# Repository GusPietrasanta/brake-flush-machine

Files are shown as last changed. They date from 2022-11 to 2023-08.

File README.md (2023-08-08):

# Brake Fluid Flush Machine

Brake Fluid Flush Machine is a personal project that was born in the need to replace an old and unfunctional PCB that controlled all the functions in an ATE FB30S.

All the mechanical parts of the machine were working perfectly, but the PCB broke down, not being able to control the output pressure anymore, going to full pressure constantly. That resulted in the necessity of a person (me, ha) continually controlling the pressure manually, simply and boringly turning the knob on and off, while flushing the brake fluid of the cars at the shop were I work.

Due to the age of the machine, spare parts are not longer available, making it impossible to buy a replacement PCB.

The original PCB had to be completely replaced for a hand-made circuit board that houses a STM32F103C6T6 (A.K.A. BluePill) as the brain of the machine. Also minor additions and modifications had to be done to the original wiring and components.

## How it works

Schematics for the wiring can be found in the schematics folder of the project (both .kicad files and screen captures for quick reference).

The C code is pretty simple and straightforward, and also heavily commented, but basically it runs a program which:

1. Includes all the start-up functions.
2. Declares 3 constants that correspond to three different settings of pressure (0.4, 1.5 and 2.2 bar) after the ADC (Analog to digital converter).
3. Sets the interval for an alarm/buzzer that is triggered when something is wrong (brake fluid tank level too low, or pressure out of normal values).
4. Initializes variables for brake fluid tank level and pressure.
5. Declares the functions to check if everything is ready to run, check level, and detect the required pressure from the knob.
6. Calls all the start-up functions (clock configuration, PWM Configuration, ADC configuration, enable and start.
7. Initilizes the variables pwm (%/duty for the pump), setPoint (or desired pressure), error (setPoint - pressure) and timerBuzzer to 0.
8. Starts the infinite loop which:
  - Checks if everything is ok to run (pressure reading and tank level).
    - If so, it turns on the safety relay that feeds the pump, checks the required pressure, calculates the adequate PWM, and sets that PWM to the output pin that controls the pump.
    - If something goes wrong, it sets the PMW to 0, turns the relay off, turns the red LED on, the green LED off, and starts a counter to turn the buzzer on and off.

## Now some images
<div align="center">
 
 ## The problem with the original circuit board.
 The old PCB was dangerously ramping the pressure up constantly beyond safe limits.
 Too much pressure
 
 ## Prototyping at home.
 Prototyping at home
  
 ## The old PCB ready to come out.
Old PCB

## The new circuit board ready to go in (not the final version sadly)
New PCB first version
 
After a couple of runs, the main transistor overheated and stopped working properly: a junction went short-circuit, sending the pump to full speed. The safety relay came into action turning the power supply off avoiding a probable explosion of the plastic reservoir for the brake fluid of the car I was working on at the moment, due to over-pressure.
  
Time to see what happened.
 
## Wrong power transistor handling = Long fall time = Overheating
  
On the first version of the circuit board I was using a pre-made MOSFET driver module that was near to its current limits, plus a way too high frequency choice to avoid noise from DC motor.
  
 Long transistor fall time

 ## Lower frequency + using an optocoupler with the right resistor = Perfect.
  
 Now with some changes done to the transistor driving circuit and modifiying the code to run the PWM at 1kHz instead of 10kHz made a nice waveform.
  
Better transistor fall time
  
 ## Fitting the new version of the circuit board.
  
  Fitting the circuit baord
  
 ## Testing the 3 different pressure settings.
  
  Testing pressure
  
## Brake fluid level in the tank going low.
  
(Note the pressure manometer dropping to 0 and the red LED turning on while the green one turns off, as well as the brake fluid stops coming out from the fitting of course).
  
  Low level testing

</div>

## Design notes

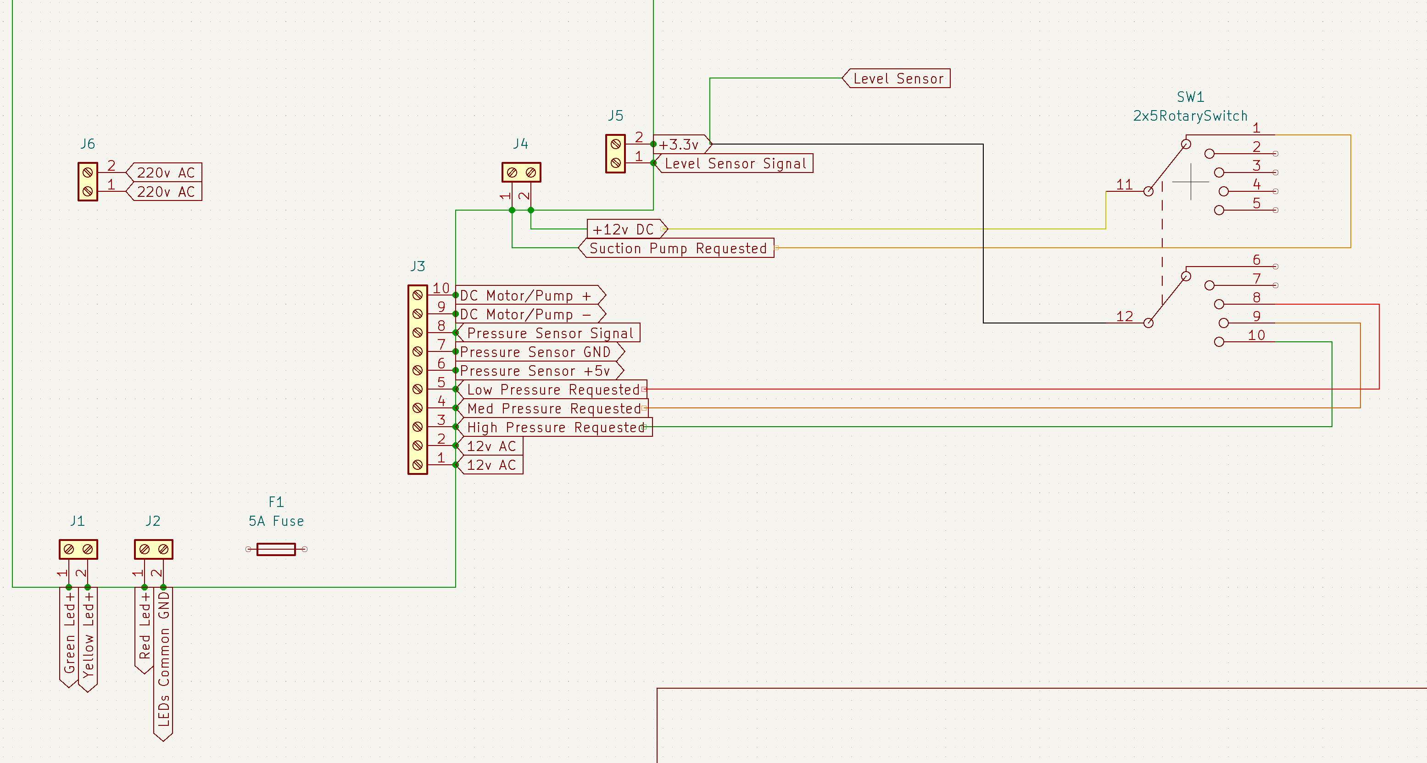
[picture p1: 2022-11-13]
schematics/PinoutBFMBoard/PinoutBFMBoard.png

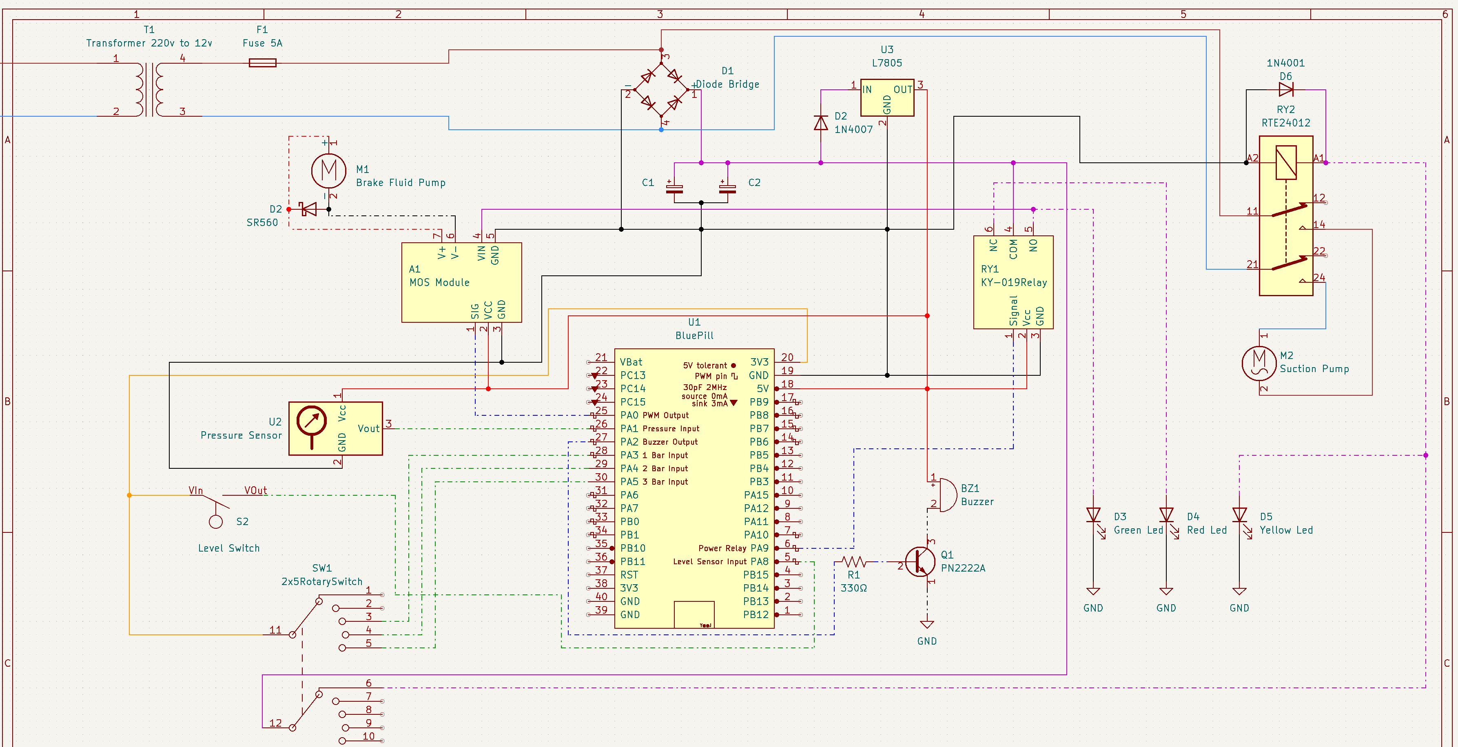
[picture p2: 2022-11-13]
schematics/BrakeFluidMachineSchematics.png

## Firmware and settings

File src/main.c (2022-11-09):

#include "includes.h"

// The next values are ADC values that correspond to 1, 2 and 3 bars of pressure.
const uint16_t oneBar = 800;
const uint16_t twoBar = 1100;
const uint16_t threeBar = 1400;

// This value stores how often the buzzer will toggle (in 10^(-4)/0.1ms increments).
const uint16_t toggleInterval = 10000;

volatile uint8_t levelOk = 0;       // Brake fluid tank level
volatile uint16_t pressure = 0;     // Process Variable/Actual Pressure

// Function that will check if everything is in order to work
uint8_t allGood(void);
// Function that will check the tank level accessing the Port A Pin 8 Input Data Register
uint8_t checkLevel(void);
// Function that will update the set point based on the position of the knob
uint16_t requiredPressure(void);

int main(void)
{
    // Initial configuration functions
  	systemClockConfig();
	pwmConfig();
	gpioConfig();
    adcConfig();
    adcEnable();
    adcStart(1);
	
	volatile uint16_t pwm = 0;          // Control Variable/PWM
    volatile uint16_t setPoint = 0;     // Set Point/Desired pressure
    volatile int16_t error = 0;         // Set Point - Process Variable
    volatile uint16_t timerBuzzer = 0;  // Counter to toggle the buzzer 

    while (1)
	{

        //levelOk = checkLevel();     // Check if the tank level is ok and set as variable

        //pressure = adcGetVal();                     // Get the actual pressure from the ADC

        // If brake fluid tank level is ok, and the pressure sensor is between expected/normal values...
        if (allGood())
        {
            TIM2->CCR3 = 0;                         // Turn the buzzer OFF

            GPIOA->ODR &= ~GPIO_ODR_ODR7;           // Turn red led OFF

            GPIOA->ODR |= GPIO_ODR_ODR6;            // Turn green led ON

            GPIOA->ODR |= GPIO_ODR_ODR9;            // Turn on the power relay that feeds the motor driver

            // While everything is in order...
            while (allGood())
            {
                setPoint = requiredPressure();          // Update the set point to the selected pressure on the machine front knob

                error = setPoint - pressure;            // Calculate the error

                pwm = error * 0.2;                      // Calculate PWM duty - 0.2 is kp/Proportional gain

                if ((pwm > 20) & (pwm < 100))
                {
                    TIM2->CCR1 = pwm;                   // Set the value calculated on pwm as the timer duty cycle
                }
                else if (pwm > 100)
                {
                    TIM2->CCR1 = 100;                   // If calculated value is bigger than 100, set it at 100% (Maximum duty)
                }
                else
                {
                    TIM2->CCR1 = 0;                     // If calculated value is smaller than 0, leave it at 0% (Minimum duty)
                }
            }
        }
        // If conditions were not met...
        else
        {
            GPIOA->ODR &= ~GPIO_ODR_ODR9;            // Turn off the power relay that feeds the motor driver

            GPIOA->ODR &= ~GPIO_ODR_ODR6;           // Turn green led ON

            GPIOA->ODR |= GPIO_ODR_ODR7;            // Turn red led OFF

            pwm = 0;                                // Set PWM to 0%

            TIM2->CCR1 = pwm;                       // Set time Duty Cycle to 0%

            timerBuzzer = toggleInterval - 500;     // Force the timer to be close to 9999 to start as soon as possible.

            /* Here I'm using Timer 2 Update Interrupt Flag as a timer. 
            I don't expect this method to be 100% accurate but it's enough to toggle...
            ... a buzzer on and off, non-blocking, and without activating another Timer.  
            TIM2 UIF is set to 1 by hardware every time TIM2 CNT reaches TIM2 ARR (100)
            Being TIM2 frequency = 1Mhz, CNT will be increased each uS, and TIM2 UIF...
            ... will be set to 1 every 100uS
            That means that every 10000 UIF events, 1 million uS/1 second has passed. */
            
            // And while tank level is low, or the pressure is out of range, simply toggle the buzzer 
            while (!(allGood()))
            {
                if (TIM2->SR & TIM_SR_UIF)              
                {
                    TIM2->SR &= ~TIM_SR_UIF;
                    
                    timerBuzzer++;
                }

                // If 1 second has passed, toggle the buzzer and reset counter/timer to 0.
                if (timerBuzzer > toggleInterval)
                {
                    if (TIM2->CCR3 != 0)
                    {
                        TIM2->CCR3 = 0;
                    }
                    else
                    {
                        TIM2->CCR3 = 50;
                    }
                timerBuzzer = 0;
                }
            }
        }
	}
}

uint8_t allGood(void)
{
    pressure = adcGetVal();     // Get the actual pressure from the ADC

    levelOk = checkLevel();     // Check if the tank level is ok

    if ((levelOk) && (pressure >= 300) && (pressure <= 2000)) 
    {
        return 1;
    }
    else
    {
        return 0;
    }
    
}

uint8_t checkLevel(void)
{
    if ((GPIOA->IDR & GPIO_IDR_IDR8) != 0)  // Read the status of the level sensor from Port A Input Data Register 8
    {
        return 1;
    }
    else
    {
        return 0;
    }
}

uint16_t requiredPressure(void)
{
    if (GPIOA->IDR & GPIO_IDR_IDR3)                 // If Pin 3 is ON
    {
        return oneBar;
    }
    else if (GPIOA->IDR & GPIO_IDR_IDR4)            // If Pin 4 is ON
    {
        return twoBar;
    }
    else if (GPIOA->IDR & GPIO_IDR_IDR5)            // If Pin 5 is ON
    {
        return threeBar;
    }
    //Otherwise, the machine is not required to work, so set the Set Point to 0
    else
    {
        return 0;
    }
}

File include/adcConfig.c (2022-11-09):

#include "stm32f103x6.h"

// Max ADC Clock frequency is 14 MHz
// ADCCLK is synchronous with PCLK2(APB2 Clock), which is set to 72MHz
// So I should use a prescaler of /6 to have the ADCCLK running at 12MHz
// Select Channel
// Conversion mode

void adcConfig(void)
{

        /*
        STEPS TO FOLLOW:
        1. Enable ADC and GPIO Clock
        2. Set the prescaler in the Common Control Register (CCR)
        3. Set the Scan Mode and resolution in the Control Register 1 (CR1)
        4. Set the Continuous Conversion, EOC, and Data Alignment in Control Red 2 (CR2)
        5. Set the Sampling Time for the cannels in ADC_SMPRx
        6. Set the Regular Channel sequence length in ADC_SQR1
        7. Set the Respective GPIO PINs in the Analog Mode
        */

    //1. Enable ADC and GPIO Clock
    // I'll enable ADC1EN
    RCC->APB2ENR |= RCC_APB2ENR_ADC1EN;


    // Port A is already ON in gpioConfig.c
    //RCC->APB2ENR |= RCC_APB2ENR_IOPAEN;


    //2. Set the prescaler in the Common Control Register (CCR)
    // ADC PRE is in RCC_CFGR
    RCC->CFGR &= ~(RCC_CFGR_ADCPRE_0);
    RCC->CFGR |= RCC_CFGR_ADCPRE_1;

    // Now move to ADC registers
    //3. Set the Scan Mode and resolution in the Control Register 1 (CR1)
    ADC1->CR1 |= ADC_CR1_SCAN;
    //In the STM32F1 there is no configuration for resolution

    //4. Set the Continuous Conversion, EOC, and Data Alignment in Control Red 2 (CR2)

    // Continuous Conversion
    ADC1->CR2 |= ADC_CR2_CONT;
    // Data Alignment
    ADC1->CR2 &= ~ (ADC_CR2_ALIGN);

    // EOC? Seems to be default to 1 on STM32F1.
    // EOC Says: End of conversion
    //This bit is set by hardware at the end of a group channel conversion 
    // (regular or injected). It is cleared by software or by reading the ADC_DR.
    
    // Set External Event Selection pointed to SWSTART bit
    ADC1->CR2 |= ADC_CR2_EXTSEL;

    //5. Set the Sampling Time for the cannels in ADC_SMPRx
    // I'll be using ADCSMP1. Clear all the bits to get 1.5 cycles of Sample Time.
    ADC1->SMPR2 &= ~(ADC_SMPR2_SMP1);

    //6. Set the Regular Channel sequence length in ADC_SQR1
    // L[3:0]: Regular channel sequence length (How many ADC Channels I'm using)
    // 0000: 1 Conversion, so lets clear all the bits to 0.
    ADC1->SQR1 &= ~((ADC_SQR1_L));

    //7. Set the Respective GPIO PINs in the Analog Mode
    GPIOA->CRL &= ~(((GPIO_CRL_CNF1)) | (GPIO_CRL_MODE1));
    ADC1->SQR3 |= (1<<0);
}

void adcEnable(void)
{
    /*
    STEPS TO FOLLOW
    1. Enable the ADC by setting ADON bit in CR2
    2. Wait for ADC to stabilize (approx 10us)
    */

   ADC1->CR2 |= ADC_CR2_ADON; // ADON = 1 Enable ADC1

    uint32_t delay = 10000;
    while (delay--);

    ADC1->CR2 |= ADC_CR2_CAL;

    uint32_t delay2 = 10000;
    while (delay2--);
}

void adcStart(int channel)
{
    /* 
    STEPS TO FOLLOW
    1. Set the channel sequence in the SQR Register
    2. Clear the Status Register
    3. Start the Conversion by settin the SWSTART bit in CR2
    */
   	ADC1->SR = 0;                      // Clear Status register
	ADC1->CR2 |= (1<<20);              // Conversion on external event enabled
	ADC1->CR2 |= 1<<22;                // Start conversion

}

void adcWaitForConv(void)
{
    // EOC Flag will be set, once the conversion is finished
    while (!(ADC1->SR & (1<<1)));
}

uint16_t adcGetVal(void)
{
    // Read the data register
    return ADC1->DR;
}

void adcDisable(void)
{
    ADC1->CR2 &= ~(1<<0); // Disable ADC
}

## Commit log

2022-11-09 Finished version of the brake fluid flush version
2022-11-09 Added electric schematics
    [BrakeFluidMachineSchematics.kicad_sch, PinoutBFMBoard.kicad_pcb, PinoutBFMBoard.kicad_sch]
2022-11-13 Added .png for schematics for easy view.
